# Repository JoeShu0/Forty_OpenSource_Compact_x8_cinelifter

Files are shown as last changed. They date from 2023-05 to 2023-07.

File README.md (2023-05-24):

## Forty
The opensource x8/x4 compact cinelifter frame 
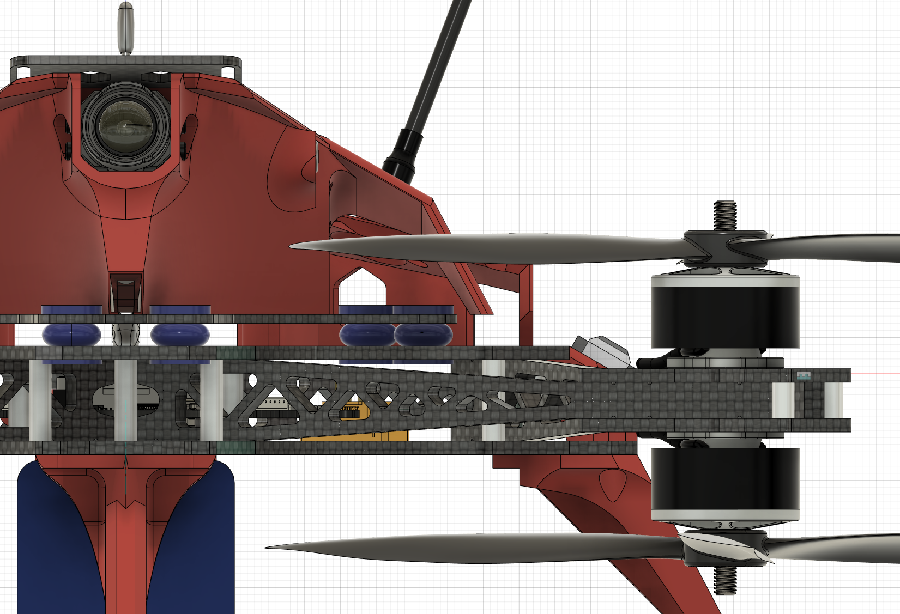
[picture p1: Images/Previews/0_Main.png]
0_Main

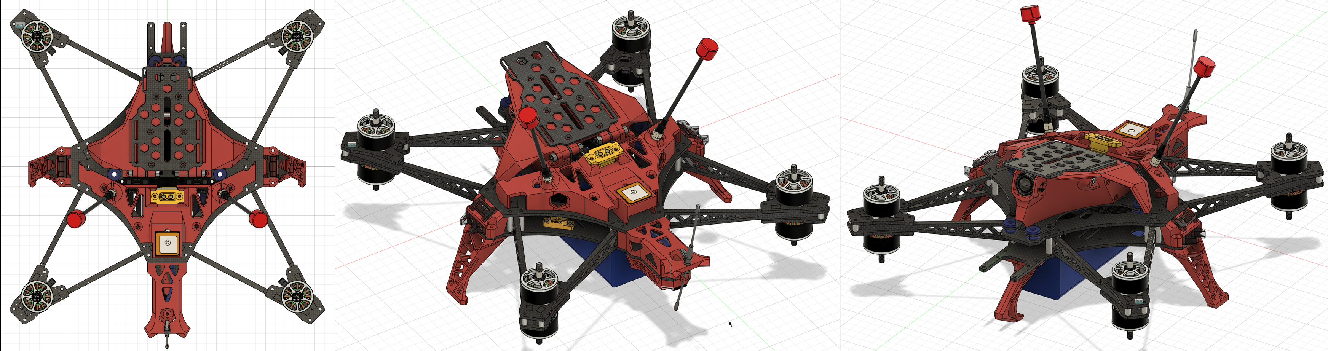
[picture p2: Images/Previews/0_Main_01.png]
0_Main_01


### Description
Forty is FPV frame designed to carry compact cinema cameras(YES, FX3! NO, FX6!), ultilizing the truss structure for maximum rigidity within reasonable weight.

Plus a sick 3dprintable super structure(v2) with transparent part and RGB LED, the performance of the machine be boosted by 20% for sure!!!(doge)

Special Thanks to **BDZZ-FPV** for helping me designing this frame!!!~

**Features are listed below:**
- Support 19x19mm motor mounting
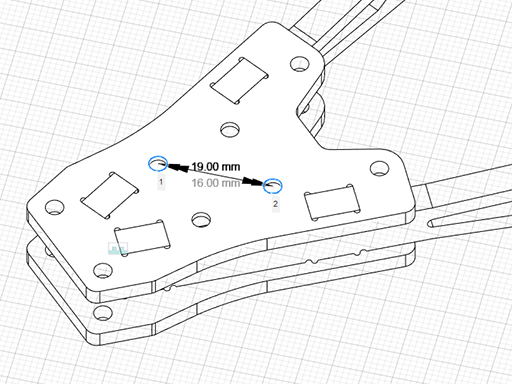
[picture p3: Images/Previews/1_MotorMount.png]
1_MotorMount
  - 
- Support up to 9 inch prop
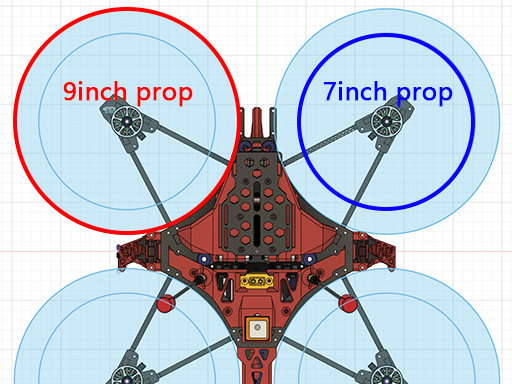
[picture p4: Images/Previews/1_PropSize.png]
1_PropSize
  - 
- Support both x8, x4 or unique x4 configuration
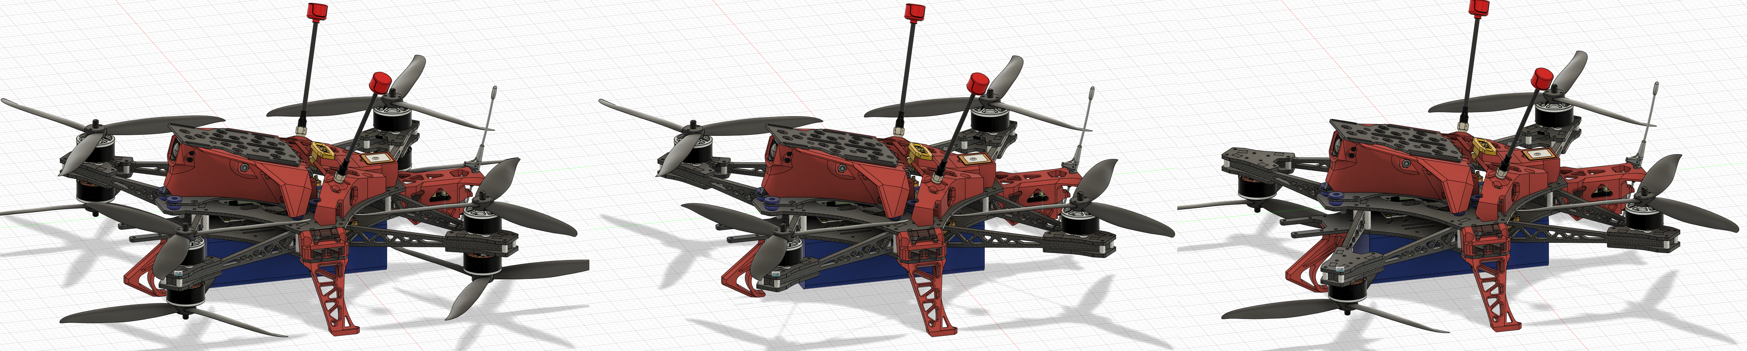
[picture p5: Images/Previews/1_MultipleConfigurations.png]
1_MultipleConfigurations
  - 
- Using truss structure with 5mx8mm arm and 3mm thick motor mount plate
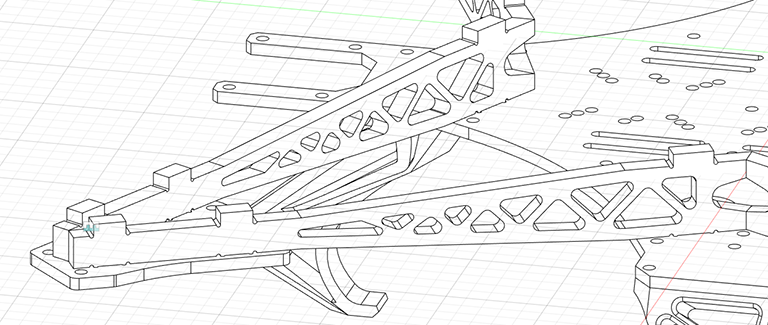
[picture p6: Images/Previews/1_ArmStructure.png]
1_ArmStructure
  - 
- 2 version of HD camera mounting options
  - 1_2HDCameraMountOptions
- 2 version of landing gear options
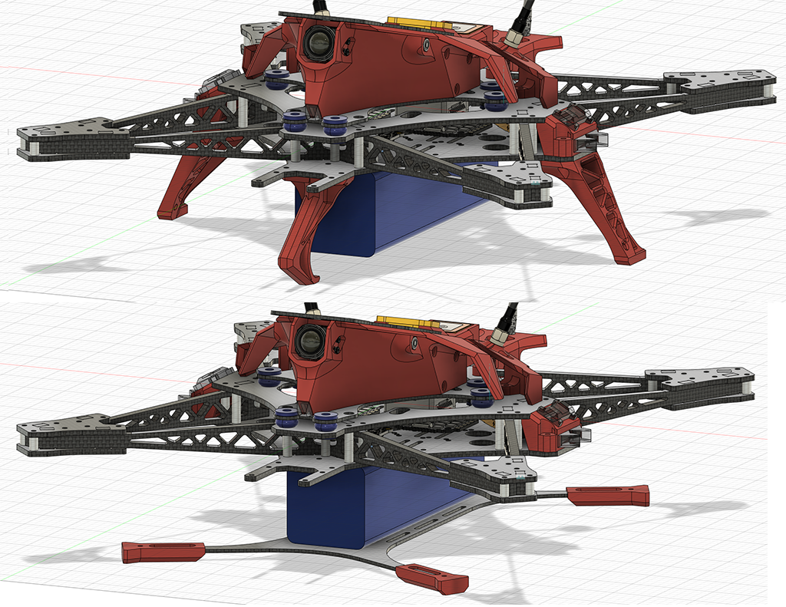
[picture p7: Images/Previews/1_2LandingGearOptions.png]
1_2LandingGearOptions
  - 
- Transparent printable part for LED lighting
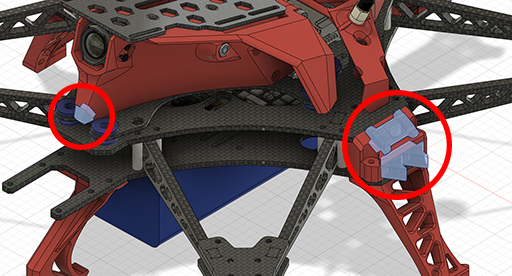
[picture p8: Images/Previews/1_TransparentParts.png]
1_TransparentParts
  - 
- Vibration absorbing balls for HD camera mounts as well as DJI O3 camera
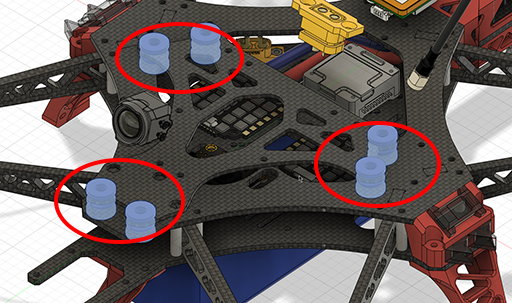
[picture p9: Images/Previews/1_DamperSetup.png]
1_DamperSetup
  - 
- Support battery sixe up to 160mmx50mm with x8 configuration, x4 configuration can carry bigger battery
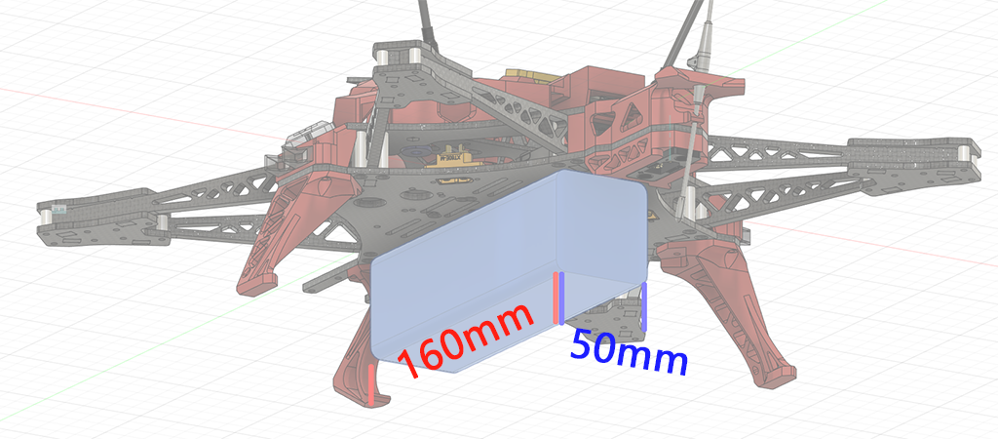
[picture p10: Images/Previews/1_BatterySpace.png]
1_BatterySpace
  - 
- Support 2 xt60 and 1 xt90 connector for different battery layouts
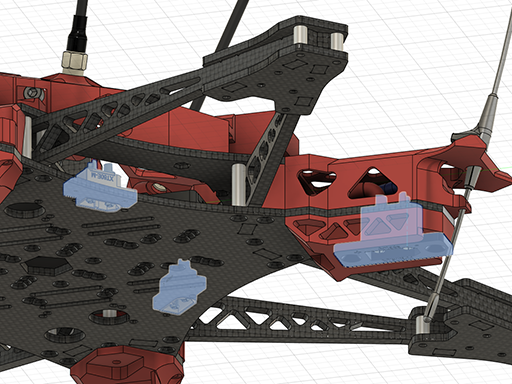
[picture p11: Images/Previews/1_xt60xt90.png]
1_xt60xt90
  - 
### Parts List

[Parts List Page](./PartsList.md)

Parts will be list for 2 versions, some parts can be shared across vesions
The main difference between these 2 versions are how HD cameras being mounted.

V1 makes everything simple and is easy for maintenance, camera angle ranges form 0 to 30, but it lacks style.
V2 is more stylized, but the printable part are all  weirdly shaped, making 3d printing them not a easy task, Some printable parts even have to take structure load. But hey, at least it looks good, right?

Due to compact design of the frame, both version don't have a big space for HD camera. So compact cinema cameras are suggested, for bigger camera like FX6 or Red komodo, **they will fit**, but watch out for **Vibration absorbing saturation** and **Prop Striking**

### Assembly Guide
if you have access to CAD programe, please download the following Step file, this will save a lot of explanation
[V1 Assembly setp file](./Parts/FullAssembly/Forty_V1.step)

[V1 Full setp file](./Parts/FullAssembly/Forty_V1_Full.step)

[V2 Assembly setp file](./Parts/FullAssembly/Forty_V2.step)

[V2 Full setp file](./Parts/FullAssembly/Forty_V2_Full.step)

Here I will just list some watch-out points when deal with this frame:

- the BasePlate has a lot 30.5x30.5mm mounting spaces, as well as some 25x25mm and some 20x20mm. so you may want spread out your electronics instead of typical flight stack
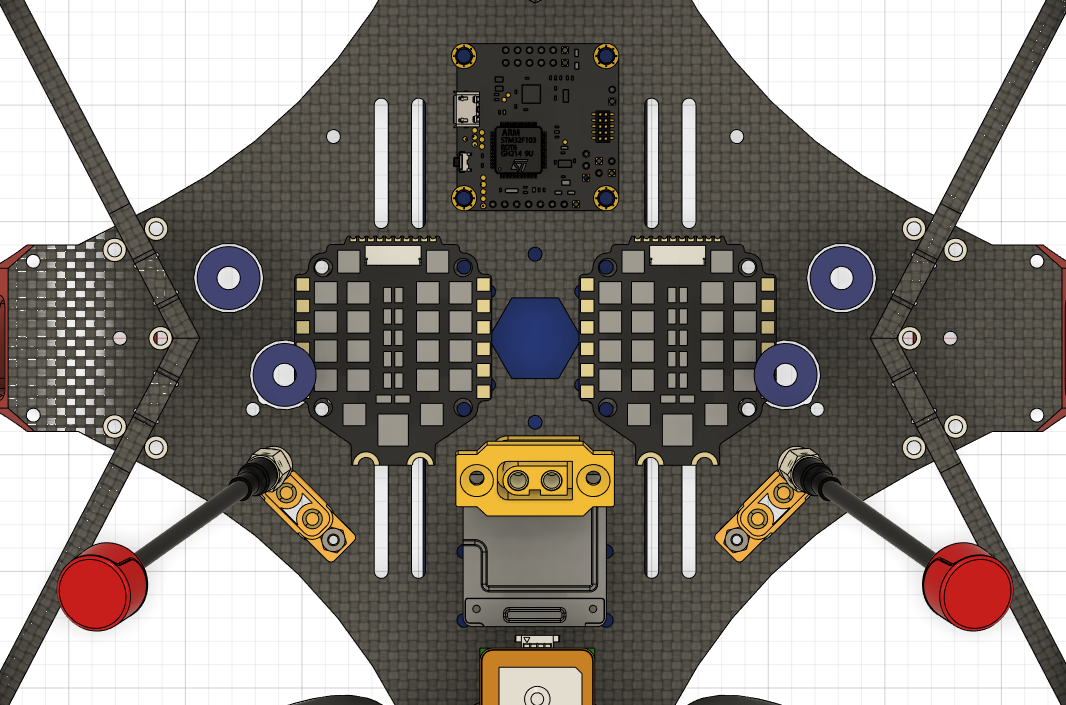
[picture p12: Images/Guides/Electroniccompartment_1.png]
Electroniccompartment_1
  - 
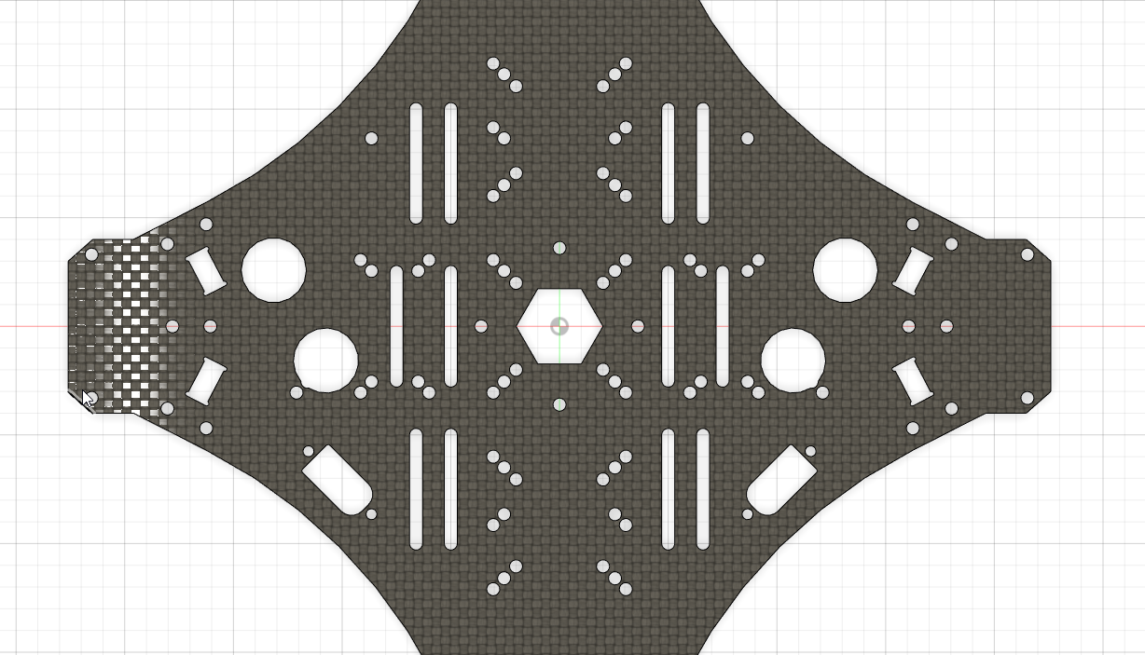
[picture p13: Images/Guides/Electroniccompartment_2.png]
Electroniccompartment_2
  - 
- Ceiling for FC and Esc compartment is pretty low, both version only have 26mm maxmium of height to work with.
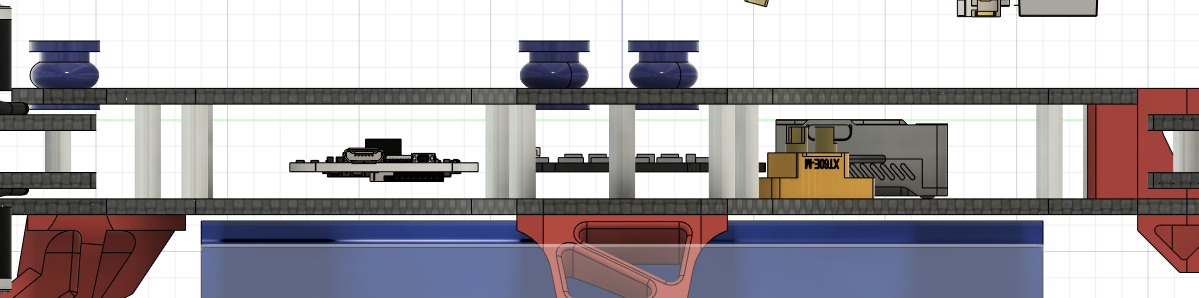
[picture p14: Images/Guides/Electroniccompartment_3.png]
Electroniccompartment_3
  - 
- If you decided to use XT90 bat for this frame, be aware the power cable will have to go throught the 2 rear arms
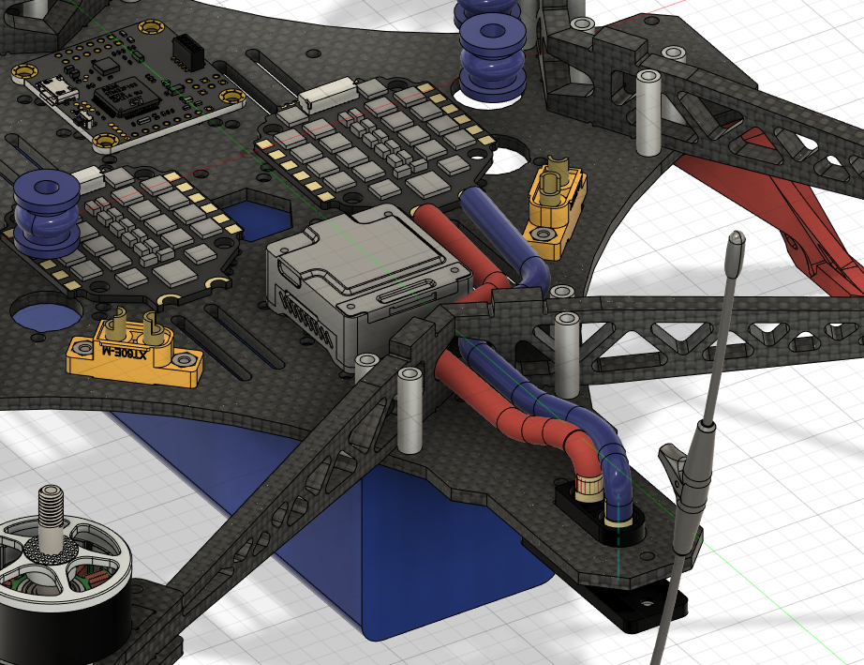
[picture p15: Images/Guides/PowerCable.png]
PowerCable
  - 
- If you decided to use 9inch prop in x8 configuration, be aware any dangling part may causing a prop strike, Due to 9inch prop on inverted motors are extremly close to both xt60 and xt90 connector.
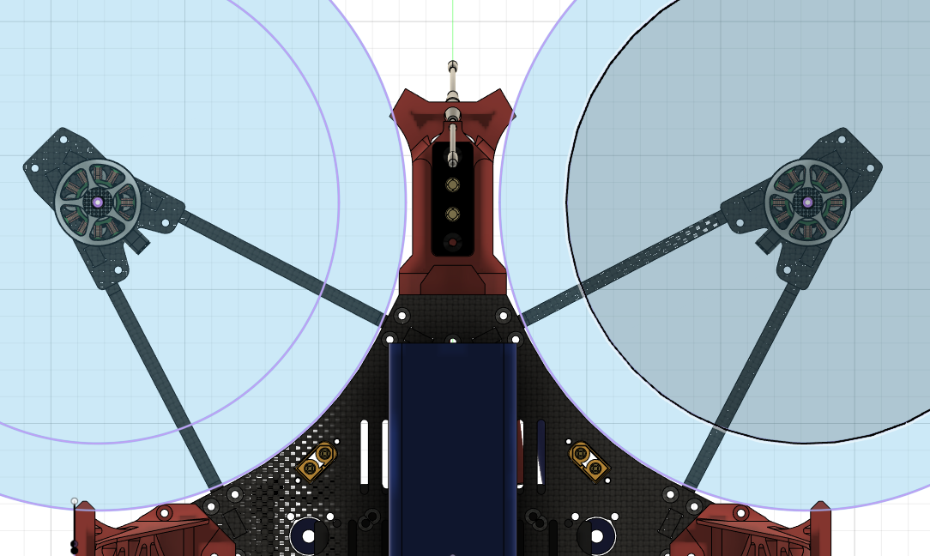
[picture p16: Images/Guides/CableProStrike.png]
CableProStrike
  - 
- If you decided to use 9inch prop, x4 configuration is suggested, If you found the Prop in HD Camera FOV, try Invert the frontal 2 motors to make the frontal prop lower, and this may improve flight efficiency a little bit~
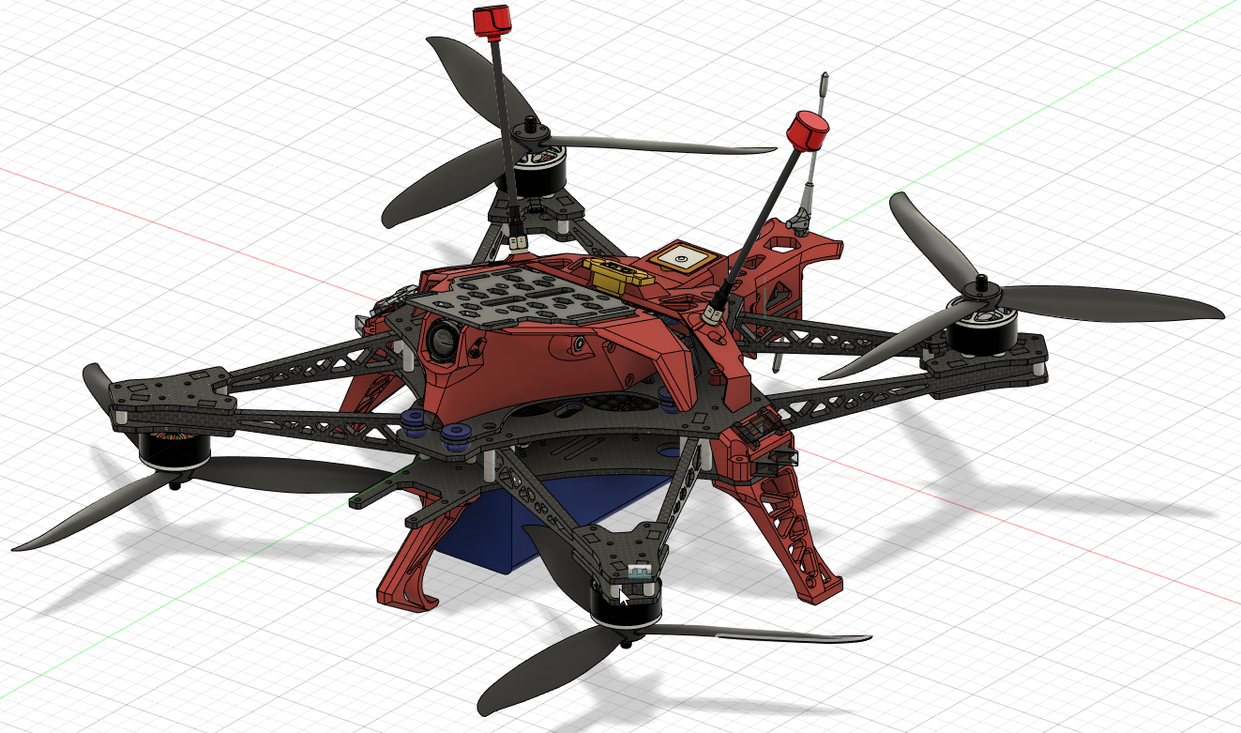
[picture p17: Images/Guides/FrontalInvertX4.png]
FrontalInvertX4
  - 
- The V2 features a closed HD camera mount, When mounting a Camera or adjusting camera angle, you have to unscrew a long M4_80, so that the whole camera supporting structure can be fliped up.
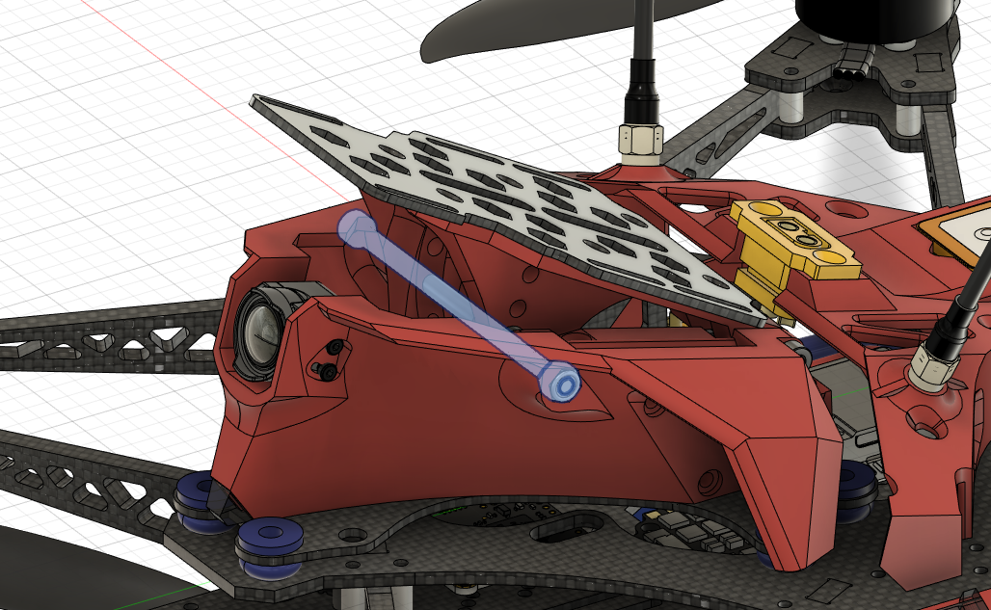
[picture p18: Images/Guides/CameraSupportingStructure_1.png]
CameraSupportingStructure_1
  - 
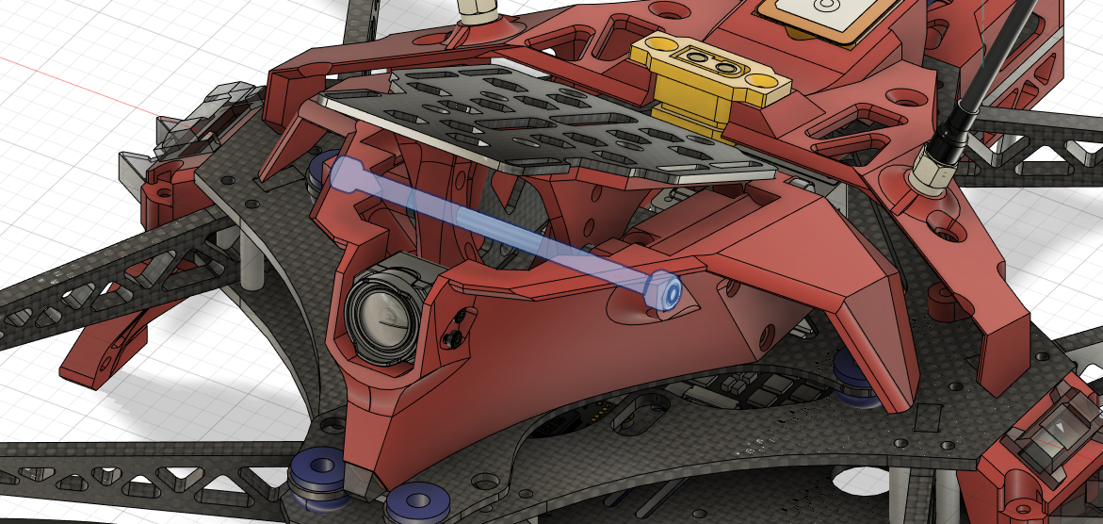
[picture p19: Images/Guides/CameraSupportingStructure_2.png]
CameraSupportingStructure_2
  - 

### Addtional

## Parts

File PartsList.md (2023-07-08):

Parts will be list for 2 versions, some parts can be shared across vesions
The main difference between these 2 versions are how HD cameras being mounted.

V1 makes everything simple and is easy for maintenance, camera angle ranges form 0 to 30, but it lacks style.
V2 is more stylized, but the printable part are all  weirdly shaped, making 3d printing them not a easy task, Some printable parts even have to take structure load. But hey, at least it looks good, right?

Due to compact design of the frame, both version don't have a big space for HD camera. So compact cinema cameras are suggested, for bigger camera like FX6 or Red komodo, **they will fit**, but watch out for **Vibration absorbing saturation** and **Prop Striking**

### FrameParts
#### shared parts
shared parts including all the base frame and landing gears
**list:**
(*part name* x *copies needed*)
**Carbon Fiber Plate**
- Arm x 8
  - Arm
- MotorMountPlate x 8
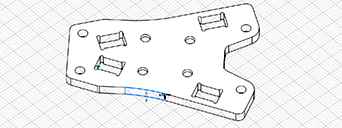
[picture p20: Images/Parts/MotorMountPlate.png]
MotorMountPlate
  - 
- BasePlate x 1
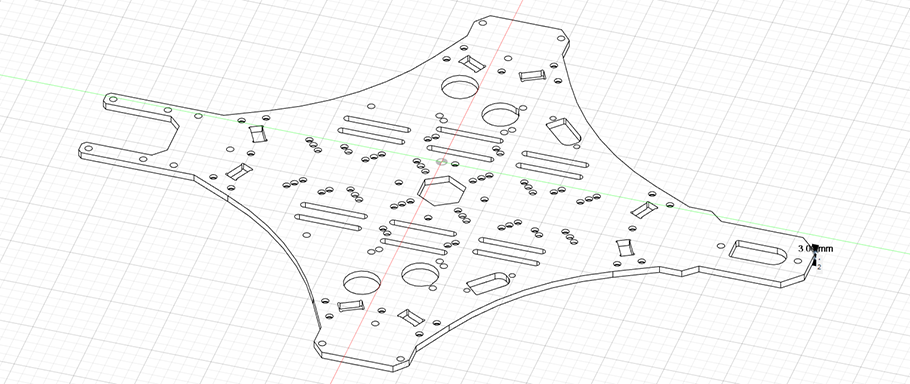
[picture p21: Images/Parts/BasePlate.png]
BasePlate
  - 
- TopPlate x 1
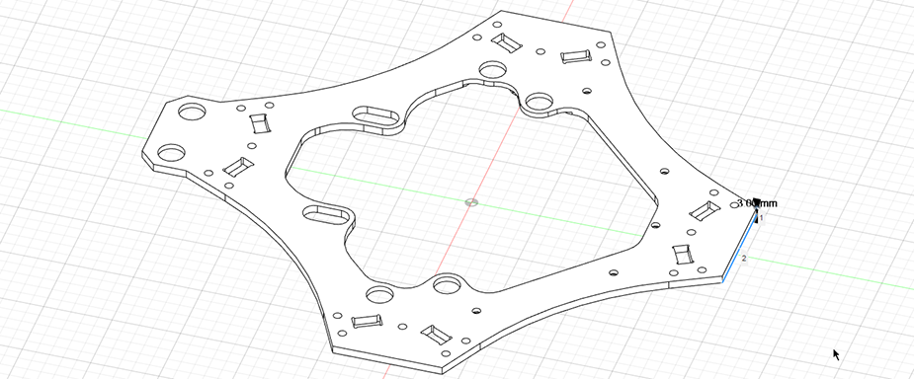
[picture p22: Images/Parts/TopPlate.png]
TopPlate
  - 

*optional:*
- BatteryLandingGear x 1
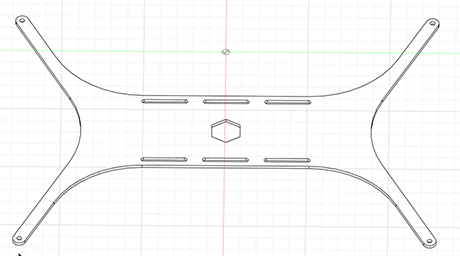
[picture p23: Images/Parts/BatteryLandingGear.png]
BatteryLandingGear
  - 

**Printable Parts**
- TM_xt90 x 1
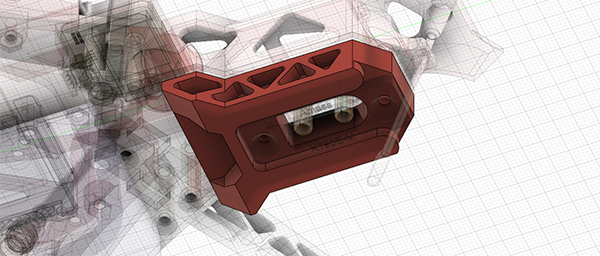
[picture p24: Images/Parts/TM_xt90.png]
TM_xt90
  - 
- TM_Topcover x 1
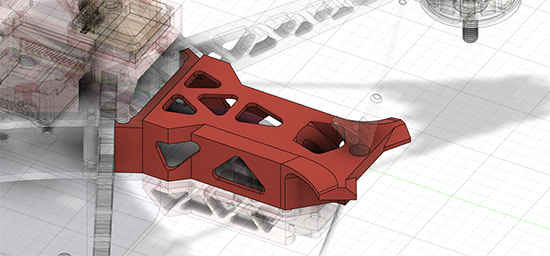
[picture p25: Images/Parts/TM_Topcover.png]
TM_Topcover
  - 

*optional:*
- BLG_Feet_3PT x 4
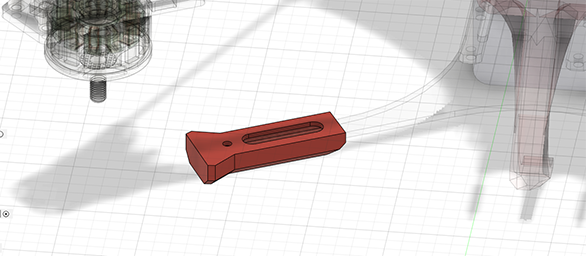
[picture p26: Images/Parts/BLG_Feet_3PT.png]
BLG_Feet_3PT
  - 
- LG_3DP_Front x 1 
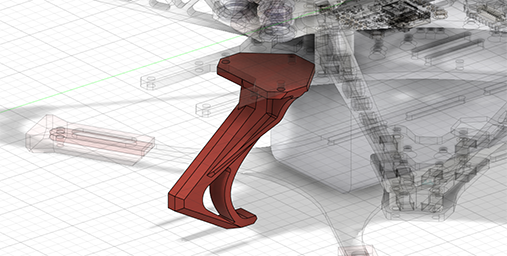
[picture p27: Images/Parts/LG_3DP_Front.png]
LG_3DP_Front
  - 
- LG_3DP_Left x 1
  - LG_3DP_Left
- LG_3DP_Right x 1
  - LG_3DP_Right

#### V1 parts
V1 parts including the simple HD Camera mount , frontal DJO O3 camera mount, side m10 GPS and SMA video ant mount.
**list:**
(*part name* x *copies needed*)
**Carbon Fiber Plate**
- CameraDamppedBasePlate x 1
  - CameraDamppedBasePlate
- CM_MountPlate x 1
  - CM_MountPlate
- CM_SupportPlate x 2
  - CM_SupportPlate
- CMB_SupportPlate x 2
  - CMB_SupportPlate

**Printable Parts**
- CM_3DP_Support01 x 2
  - CM_3DP_Support01
- CM_3DP_Support02 x 2
  - CM_3DP_Support02
- CMB_3DP_Support x 1
  - CMB_3DP_Support
- Hull_01 x 1
  - Hull_01
- M10_25mm_SMA x 1
  - M10_25mm_SMA
- TBS_Ant_SMA x 1
  - TBS_Ant_SMA
- O3CM_Left x 1
- O3CM_Right x 1
  - O3CM

#### V2 parts
V1 parts is for someone who want unique look
Including a little more aerodynamic HD camera mount, a sick back hull to mount gps, video Ant and two LED shoulders
**list:**
(*part name* x *copies needed*)
**Carbon Fiber Plate**
- CameraDamppedBasePlate02 x 1
  - CameraDamppedBasePlate02
- H02_CameraMountPlate x 1
  - H02_CameraMountPlate
- H02_support01 x 2
  - H02_support01

**Printable Parts**
- H02_FrontalShell x 1
  - H02_FrontalShell
- H02_CameraMount x 1
  - H02_CameraMount
- H02_BackCover x 1
  - H02_BackCover
- H02_Transparent x 1
  - H02_Transparent
- SH_Mount_L x 1
- SH_Mount_R x 1
  - SH_Mount
- SH_Transparent_Low_L x 1
- SH_Transparent_Low_R x 1
  - SH_Transparent_Low
- SH_Transparent_Top_L x 1
- SH_Transparent_Top_R x 1
  - SH_Transparent_Top

### Other Important Parts
Only for V2
### bolts
this frame uses m3 and m4 bolt and nuts
- main body
  - m3x18mm stand_offs (outter diameter 5mm) x 20 
  - m3x8mm sunk_head_bolt x 40
  - m3 sunk_head_washer x20
- motor plate
  - m3x8mm stand_offs (outter diameter 5mm) x 16 (12 if using v1.1 motor plate)
  - m3x6mm sun_khead_bolt x 32 (24 if using v1.1 motor plate)
- XT90EM mount
  - m3x16mm sunk_head_bolt x 1
  - m3x25mm sunk_head_bolt x 1
  - m3 self_lock_nut x 2
- XT60EM mount
  - m2.6x6mm sunk_head_bolt x 4
- landing gear
  - m3 self_lock_nut x 5
  - m3x20mm sunk_head_bolt x 4
  - m3x10mm sunk_head_bolt x 9
- back cover mount
  - m3x10mm sunk_head_bolt x 4
  - m3 self_lock_nut x 4
- frontal shell mount
  - m3x20mm sunk_head_bolt x 4
  - m3x40mm sunk_head_bolt x 2
  - m3x12mm sunk_head_bolt x 2
  - m3 self_lock_nut x 8
-frontal shell inner plate mount
  - m3x25mm sunk_head_bolt x 6
  - m3 self_lock_nut x 6
- camera mount hinge
  - m4x22mm bolt x 2
  - m4x85mm bolt x 2
  - m4 self_lock_nut x 3
- camera plate mount
  - m3x8mm sunk_head_bolt x 2
  - m3x12mm sunk_head_bolt x 2
  - m3x35mm sunk_head_bolt x 2
  - m3 self_lock_nut x 6
### motors
- brotherhobby 2812 900kv motor x 8
### miscs
- xt90em x 1
- xt60em x 2
- DJI O3 air unit x 1
- Ipex to SMA 150mm extention cord x2
- LHCP Rush Cherry Long SMA x 2
- Vibration Damping Balls 300g x 6
- MicroAir M10 GPS 25mmx25mmx8mm  x 1
- TBS CRSF Receiver x 1
- flight controller (support 8 motor out) x 1
- 4 in 1 ESC x 2 or * in 1 ESC x 1
- BAT straps 250mm -x 3
### optional
- ws2812 LEDs

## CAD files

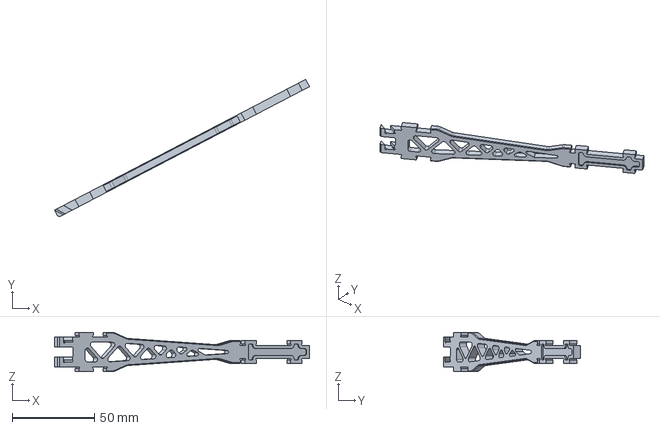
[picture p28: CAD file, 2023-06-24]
Parts/SharedParts/CarrbonFiberPlate/Arm_v1.1_B.step
155.3 x 83.6 x 24.0 mm

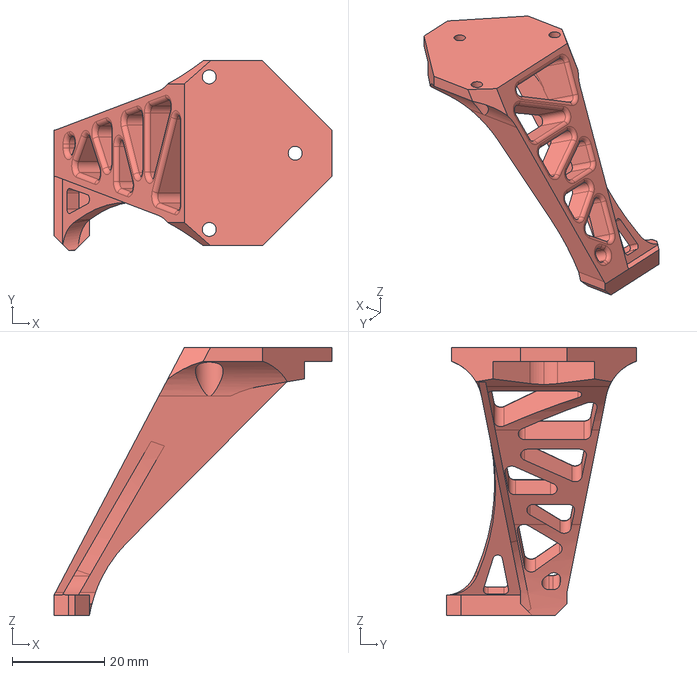
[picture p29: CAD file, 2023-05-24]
Parts/SharedParts/PrintParts/LG_3DP_Left.step
60.1 x 41.0 x 58.0 mm

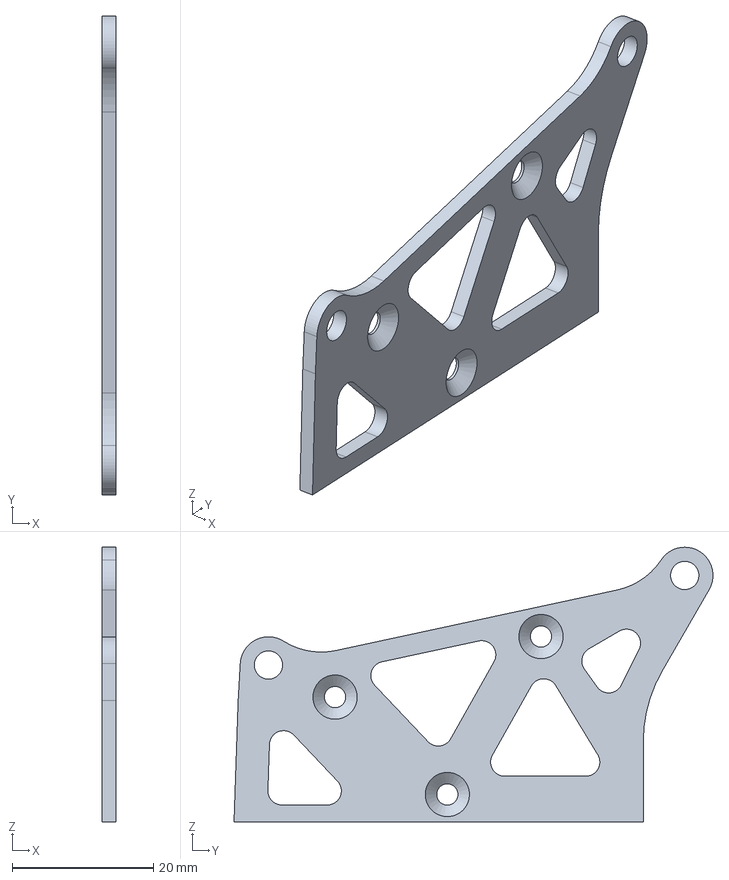
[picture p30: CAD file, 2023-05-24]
Parts/V2_Parts/CarrbonFiberPlate/H02_support01.step
2.00 x 67.8 x 38.9 mm

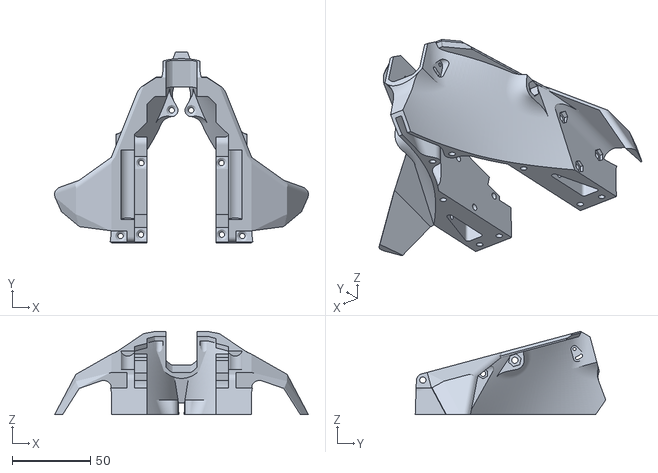
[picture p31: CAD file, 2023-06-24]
Parts/V2_Parts/PrintParts/H02_FrontalShell_v1.1.stl
162.6 x 122.0 x 53.4

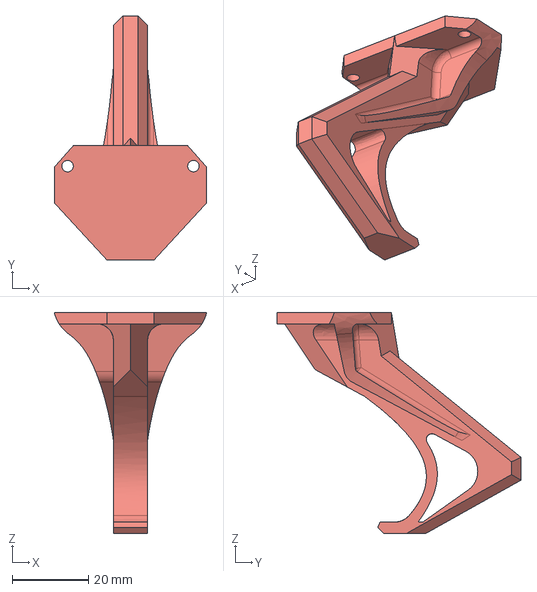
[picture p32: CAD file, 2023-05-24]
Parts/SharedParts/PrintParts/LG_3DP_Front.step
40.0 x 64.0 x 58.0 mm

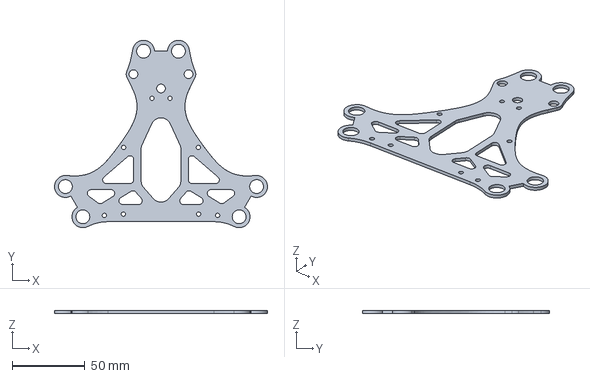
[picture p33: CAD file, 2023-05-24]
Parts/V2_Parts/CarrbonFiberPlate/CameraDamppedBasePlate02.step
146.4 x 128.8 x 2.00 mm

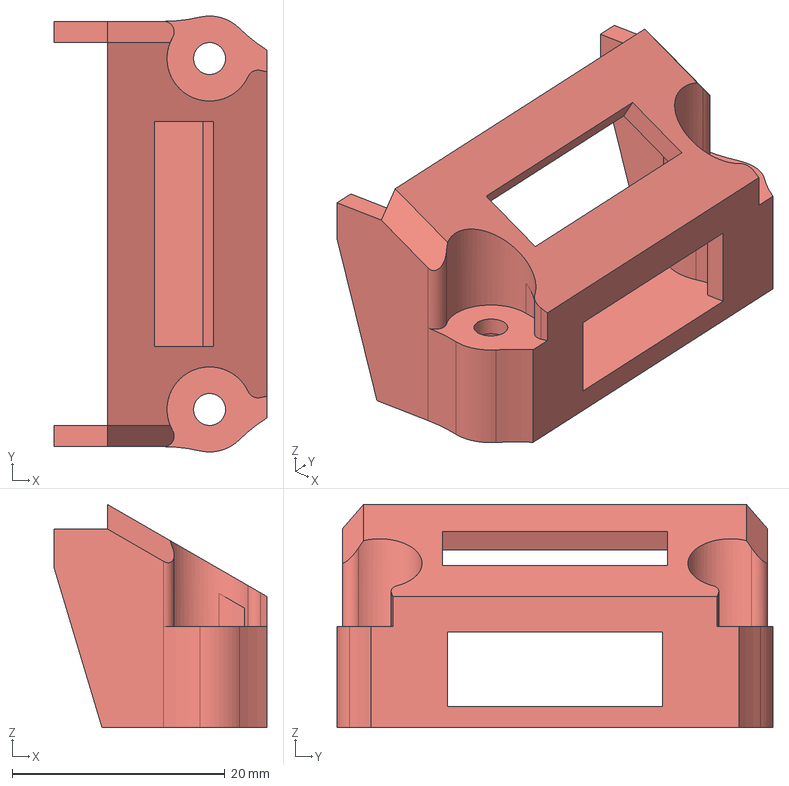
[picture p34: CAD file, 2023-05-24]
Parts/V2_Parts/PrintParts/SH_Mount_R.step
20.0 x 41.0 x 21.0 mm

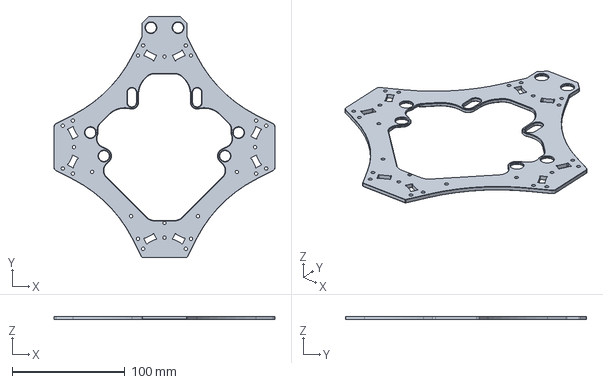
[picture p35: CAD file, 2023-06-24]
Parts/SharedParts/CarrbonFiberPlate/TopPlate_v1.1.step
196.0 x 214.0 x 3.00 mm

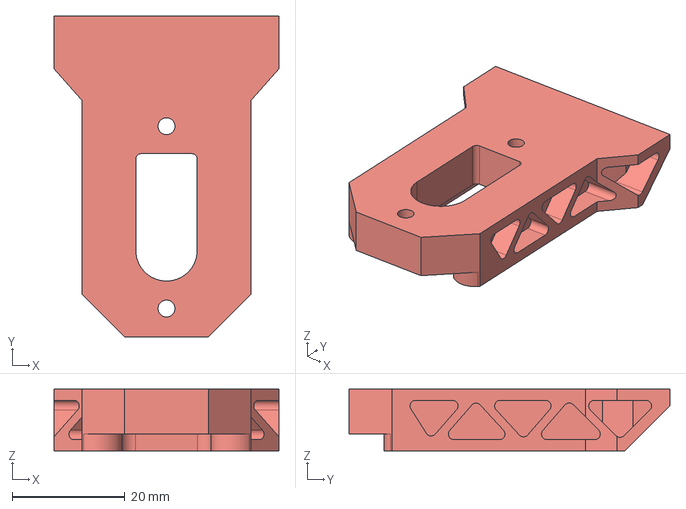
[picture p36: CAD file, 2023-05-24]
Parts/SharedParts/PrintParts/TM_xt90.step
40.0 x 57.0 x 11.0 mm

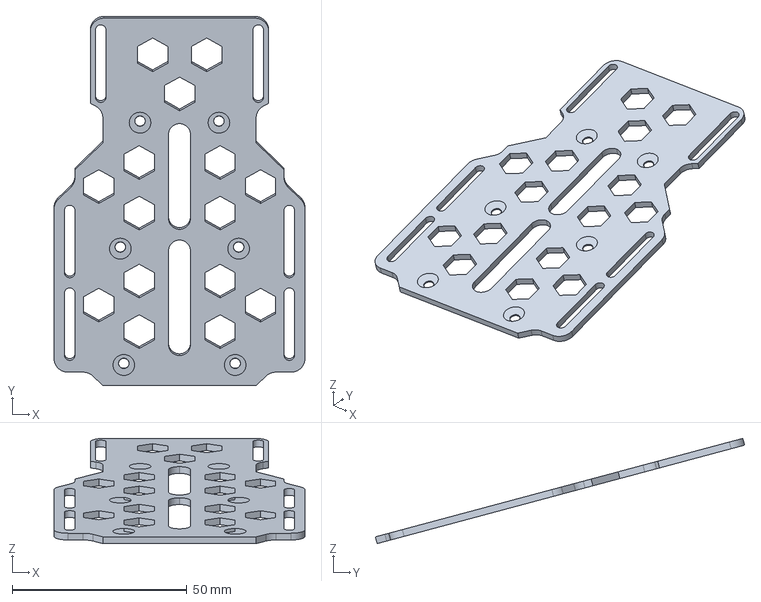
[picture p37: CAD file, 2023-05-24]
Parts/V2_Parts/CarrbonFiberPlate/H02_CameraMountPlate.step
71.9 x 105.8 x 30.1 mm

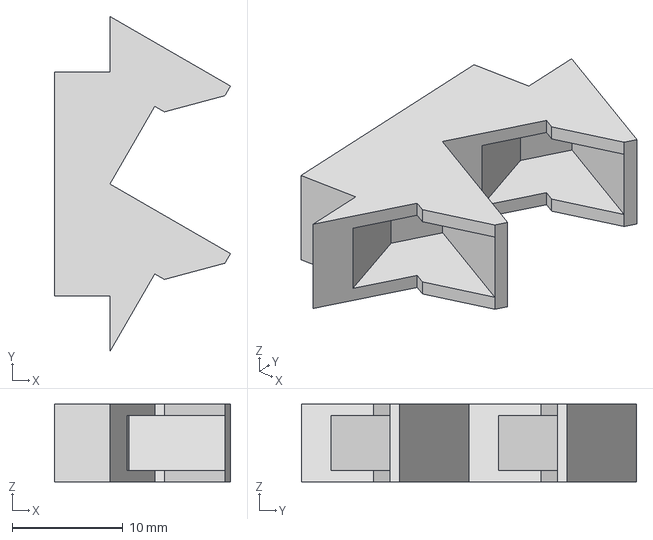
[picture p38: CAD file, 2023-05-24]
Parts/V2_Parts/PrintParts/SH_Transparent_Low_R.step
15.9 x 30.2 x 7.00 mm

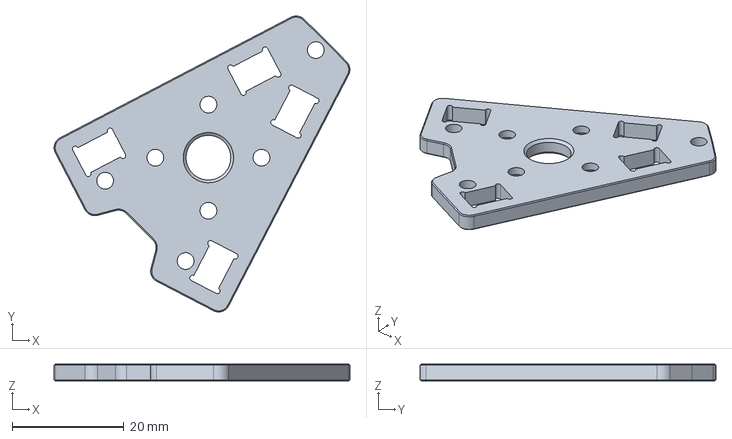
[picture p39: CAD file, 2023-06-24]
Parts/SharedParts/CarrbonFiberPlate/MotorMountPlate_v1.1.step
53.0 x 53.0 x 3.00 mm

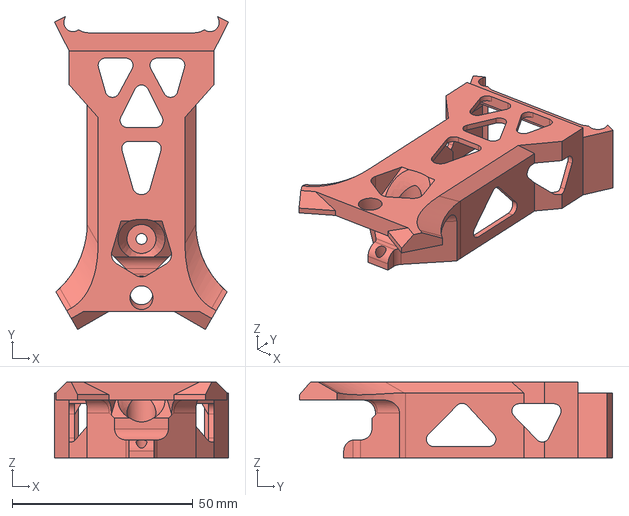
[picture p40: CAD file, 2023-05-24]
Parts/SharedParts/PrintParts/TM_Topcover.step
48.1 x 86.5 x 21.0 mm

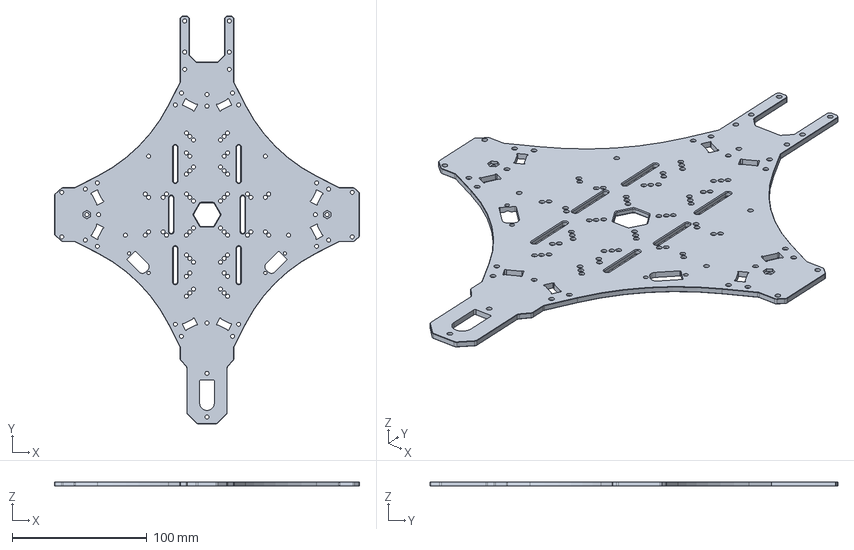
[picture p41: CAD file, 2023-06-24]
Parts/SharedParts/CarrbonFiberPlate/BasePlate_v1.1.step
226.0 x 302.0 x 3.00 mm

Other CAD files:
Parts/SharedParts/CarrbonFiberPlate/Arm_v1.1_A.step
Parts/V2_Parts/PrintParts/SH_Mount_L.step
Parts/SharedParts/PrintParts/LG_3DP_Right.step
Parts/V2_Parts/PrintParts/H02_BackCover.step
Parts/SharedParts/CarrbonFiberPlate/Arm.step
Parts/SharedParts/CarrbonFiberPlate/BasePlate.step
Parts/SharedParts/CarrbonFiberPlate/BatteryLandingGear.step
Parts/SharedParts/CarrbonFiberPlate/MotorMountPlate.step
Parts/SharedParts/CarrbonFiberPlate/TopPlate.step
Parts/SharedParts/PrintParts/BLG_Feet_3PT.step
Parts/SharedParts/PrintParts/BLG_Feet_3PT.stl
Parts/SharedParts/PrintParts/LG_3DP_Front.stl
Parts/SharedParts/PrintParts/LG_3DP_Left.stl
Parts/SharedParts/PrintParts/LG_3DP_Right.stl
Parts/SharedParts/PrintParts/TM_Topcover.stl
Parts/SharedParts/PrintParts/TM_xt90.stl
Parts/V1_Parts/CarrbonFiberPlate/CMB_SupportPlate.step
Parts/V1_Parts/CarrbonFiberPlate/CM_MountPlate.step
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

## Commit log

2023-05-24 Upload First Version
    [Arm.step, BLG_Feet_3PT.step, BLG_Feet_3PT.stl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]
2023-06-24 adding v1.1 parts
    [Arm_v1.1_A.step, Arm_v1.1_B.step, BasePlate_v1.1.step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]
